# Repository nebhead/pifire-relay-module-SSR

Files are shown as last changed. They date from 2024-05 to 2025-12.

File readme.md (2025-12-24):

# PiFire Solid State Relay (SSR) Module PCB (v1.0.2) KiCad Files

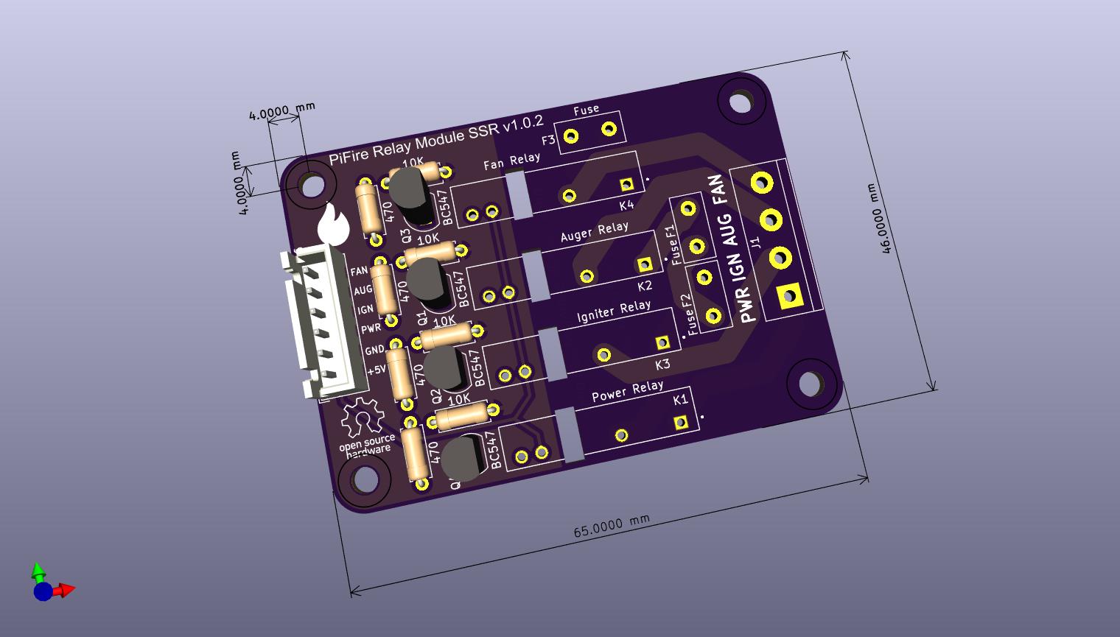
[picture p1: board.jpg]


## What is this? 

This PCB is designed to support mechanical relays for controlling incoming Power(L) to the Igniter, Auger, and AC Fan.  This board uses compact solid state relays that are able to handle high power. This is an alternative to using an off the shelf relay module which simplifies the wiring and even allows you to use the OEM harness.  

The design intent for this board was to make a DIY accessible PCB that can be more easily put together by the maker/enthusiast of almost any skill level.  Full size components are used in most cases and most (if not all) parts should be readily available to order online.  See the [Interactive BOM](#interactive-bom) for more details about the parts used and links to order.

### What is PiFire? 

PiFire is a SBC based Pellet Smoker Controller.  More details can be found [here](https://nebhead.github.io/PiFire) or [at the GitHub repo](https://github.com/nebhead/pifire). 

## What's in this Repository?

### KiCad Project Files 
In this repository you will find the latest KiCad design files for the  PCB.  Simply load the project file (.kicad_pro) into the KiCad software and you should be able to edit as needed.  Or if you just want to get this board made, jump to the production section below.

### Interactive BOM

There is an interactive BOM located in the [/bom](bom/) folder which details the parts and provides some pin information as well.  Use this to gather the components you may need to build this board out and refer back to it for placement help.    

[BOM + Pin Info](https://nebhead.github.io/pifire-relay-module-SSR)

_This is a standalone HTML file that was autogenerated by the excellent plugin for KiCad. See the plugin here: [https://github.com/openscopeproject/InteractiveHtmlBom](https://github.com/openscopeproject/InteractiveHtmlBom)_

### PDF of the Schematic

Preview the schematic in PDF format here: [Schematic](schematic.pdf)

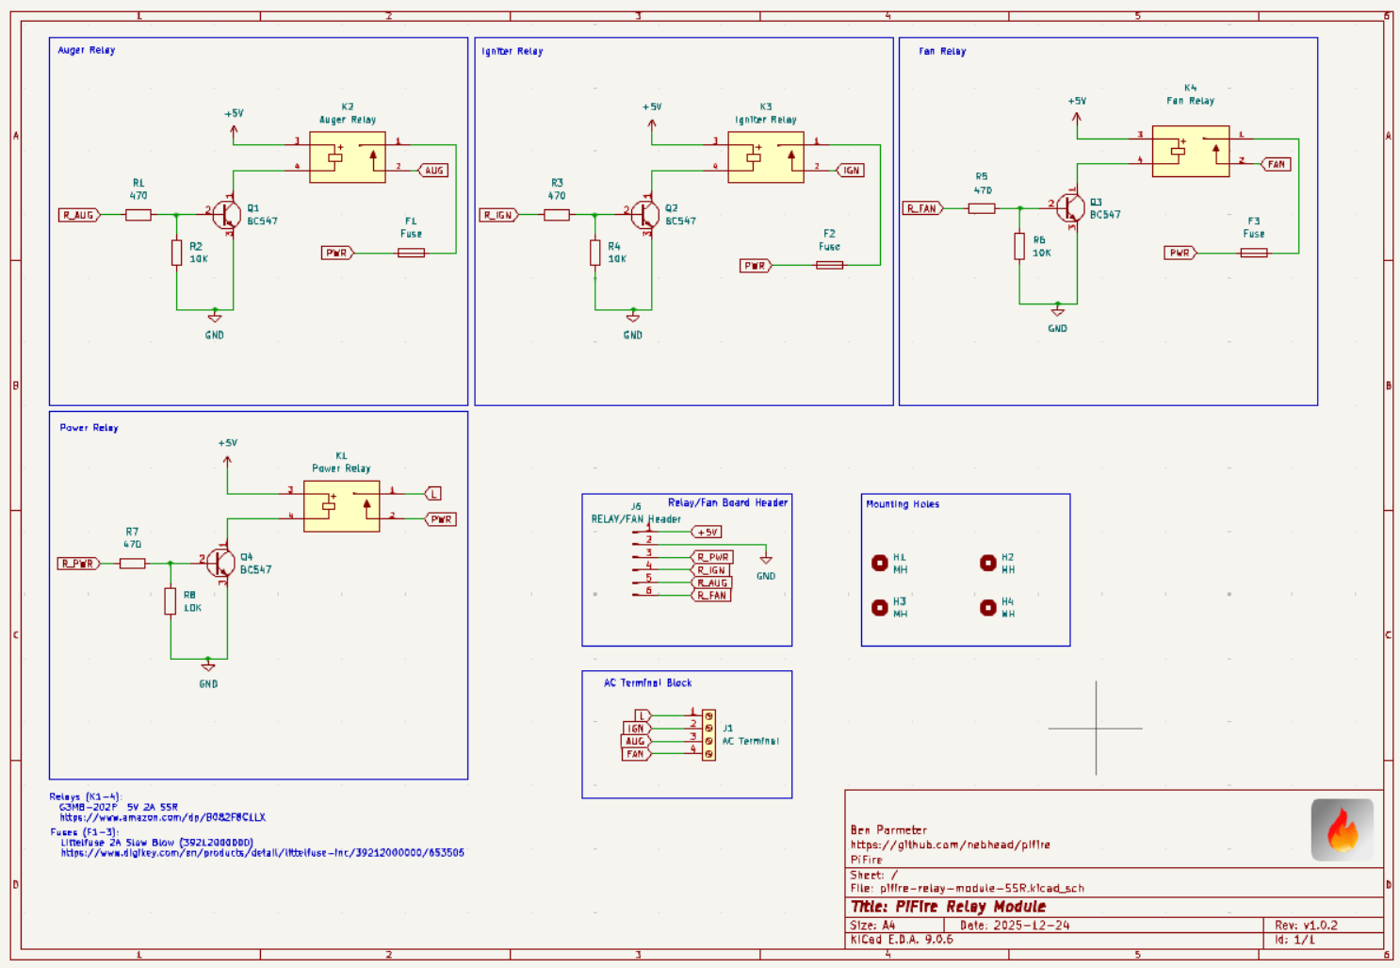
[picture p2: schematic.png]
Schematic PNG


### JLCPCB Production Files

If you wish to get these PCBs made by JLCPCB, the production files are provided in the `/production` folder.  For convenience, the file `production.zip` can simply be uploaded to JLCPCB to make it super easy to order boards.

Drop the zip file onto the order page, wait for it to upload then simply continue to order the board.  Optionally, select different board color, PCB quantity, surface finish, etc.  Most of the default settings should be sufficient. 

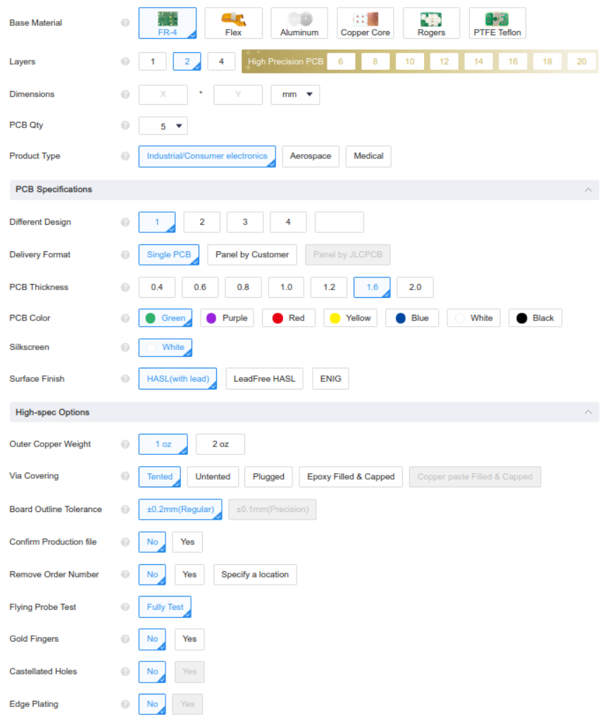
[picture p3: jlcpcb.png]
JLCPCB Order Page


### Links to the PCBs in this family of PiFire Boards

This PCB is part of a family of PCBs that can be used together to create  a full PiFire system.  Generally speaking you need the Main Module/Board, a Relay Control Board and a Probe Device board to have a basic PiFire system.  

**Main Module/Board** (required)
* [Main Board v4.0.x](https://github.com/nebhead/pifire-main-module-nopwr)

**Relay/Fan Control Boards** (choose one)
* [Mechanical Relay Module](https://github.com/nebhead/pifire-relay-module)
* [Solid State Relay Module](https://github.com/nebhead/pifire-relay-module-ssr)
* [Solid State Relay + PWM Fan Module](https://github.com/nebhead/pifire-relay-pwm-module-ssr) - Original Design
* [Solid State Relay + PWM Fan Module Alternate](https://github.com/nebhead/pifire-relay-pwm-module-ssr-alt) - Updated Design (Designed with help from @labmonkeyrat on Discord)

**Probe Device Board** (optional)
* [ADS Board](https://github.com/nebhead/pifire-ads-board) 

### 3D Printable Enclosures/Boxes 

With all of the 3D Prints for PiFire, a higher temperature filament such as PETG should be used.  PLA generally won't stand up to the temperatures that the components may be exposed to outdoors and near a hot smoker.  

#### Enclosure

Included here is an initial revision of the enclosure for this PCB.  The current models should be considered still in development and may have alignment challenges, etc. 

Except for the mounting wings, the majority of bolts to be used with this enclosure are M3. 

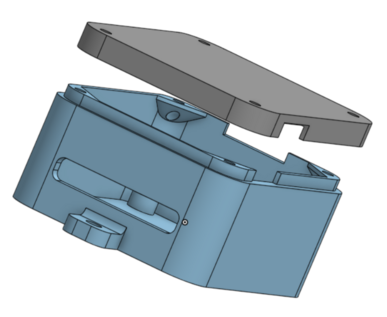
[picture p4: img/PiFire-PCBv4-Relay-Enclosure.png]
Enclosure


* STL: [Base](/printables/PiFire-v4-Relay-Base.stl)
* STL: [Lid](/printables/PiFire-v4-Relay-Lid.stl)
* OnShape: [Enclosure Original Models](https://cad.onshape.com/documents/03559f76f7adf190bf6f1259/w/7529cb0e4cd69db1a6a15202/e/07d5f9d46dc8f2b9e7dd655f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)

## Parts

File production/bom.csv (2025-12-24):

Designator | Footprint | Quantity | Value | LCSC Part #
F1, F2, F3 | Fuse_Littelfuse_395Series | 3 | Fuse
H1, H2, H3, H4 | MountingHole_3.2mm_M3 | 4 | MH
J1 | TerminalBlock_bornier-4_P5.08mm | 1 | AC Terminal
J6 | JST_XH_B6B-XH-A_1x06_P2.50mm_Vertical | 1 | RELAY/FAN Header
K1 | RELAY_G3MB-202PDC5 | 1 | Power Relay
K2 | RELAY_G3MB-202PDC5 | 1 | Auger Relay
K3 | RELAY_G3MB-202PDC5 | 1 | Igniter Relay
K4 | RELAY_G3MB-202PDC5 | 1 | Fan Relay
Q1, Q2, Q3, Q4 | TO-92L_Inline | 4 | BC547
R1, R3, R5, R7 | R_Axial_DIN0207_L6.3mm_D2.5mm_P7.62mm_Horizontal | 4 | 470
R2, R4, R6, R8 | R_Axial_DIN0207_L6.3mm_D2.5mm_P7.62mm_Horizontal | 4 | 10K

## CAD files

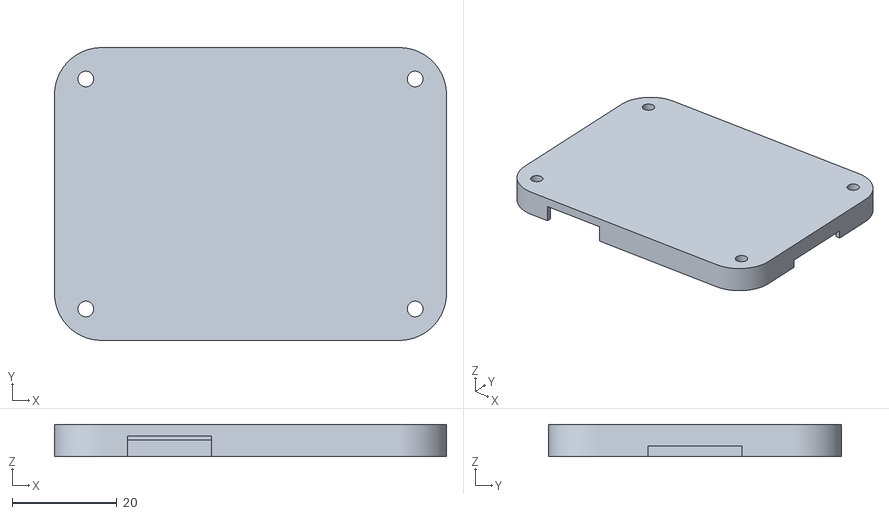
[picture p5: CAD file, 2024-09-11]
printables/PiFire-v4-Relay-Lid.stl
75.0 x 56.0 x 6.20

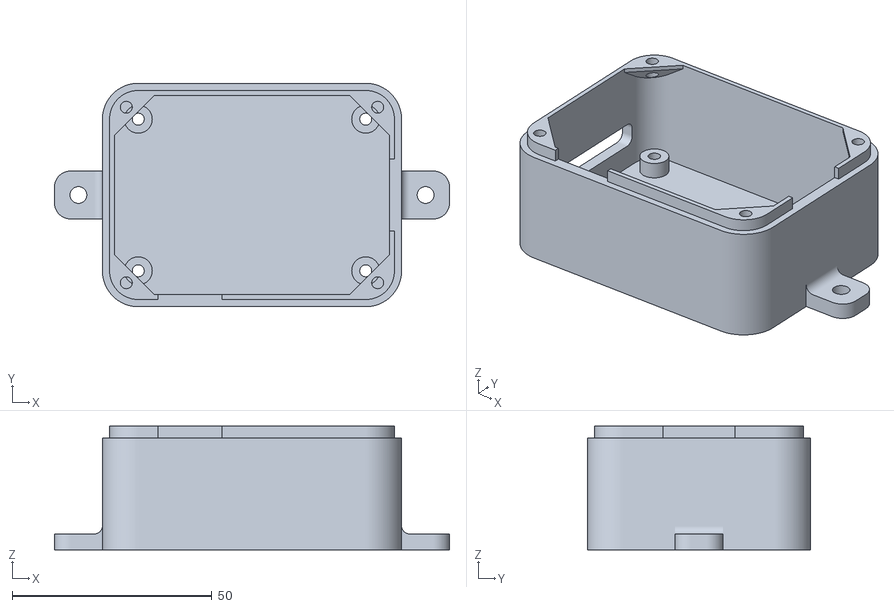
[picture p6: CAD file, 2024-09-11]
printables/PiFire-v4-Relay-Base.stl
99.0 x 56.0 x 31.0

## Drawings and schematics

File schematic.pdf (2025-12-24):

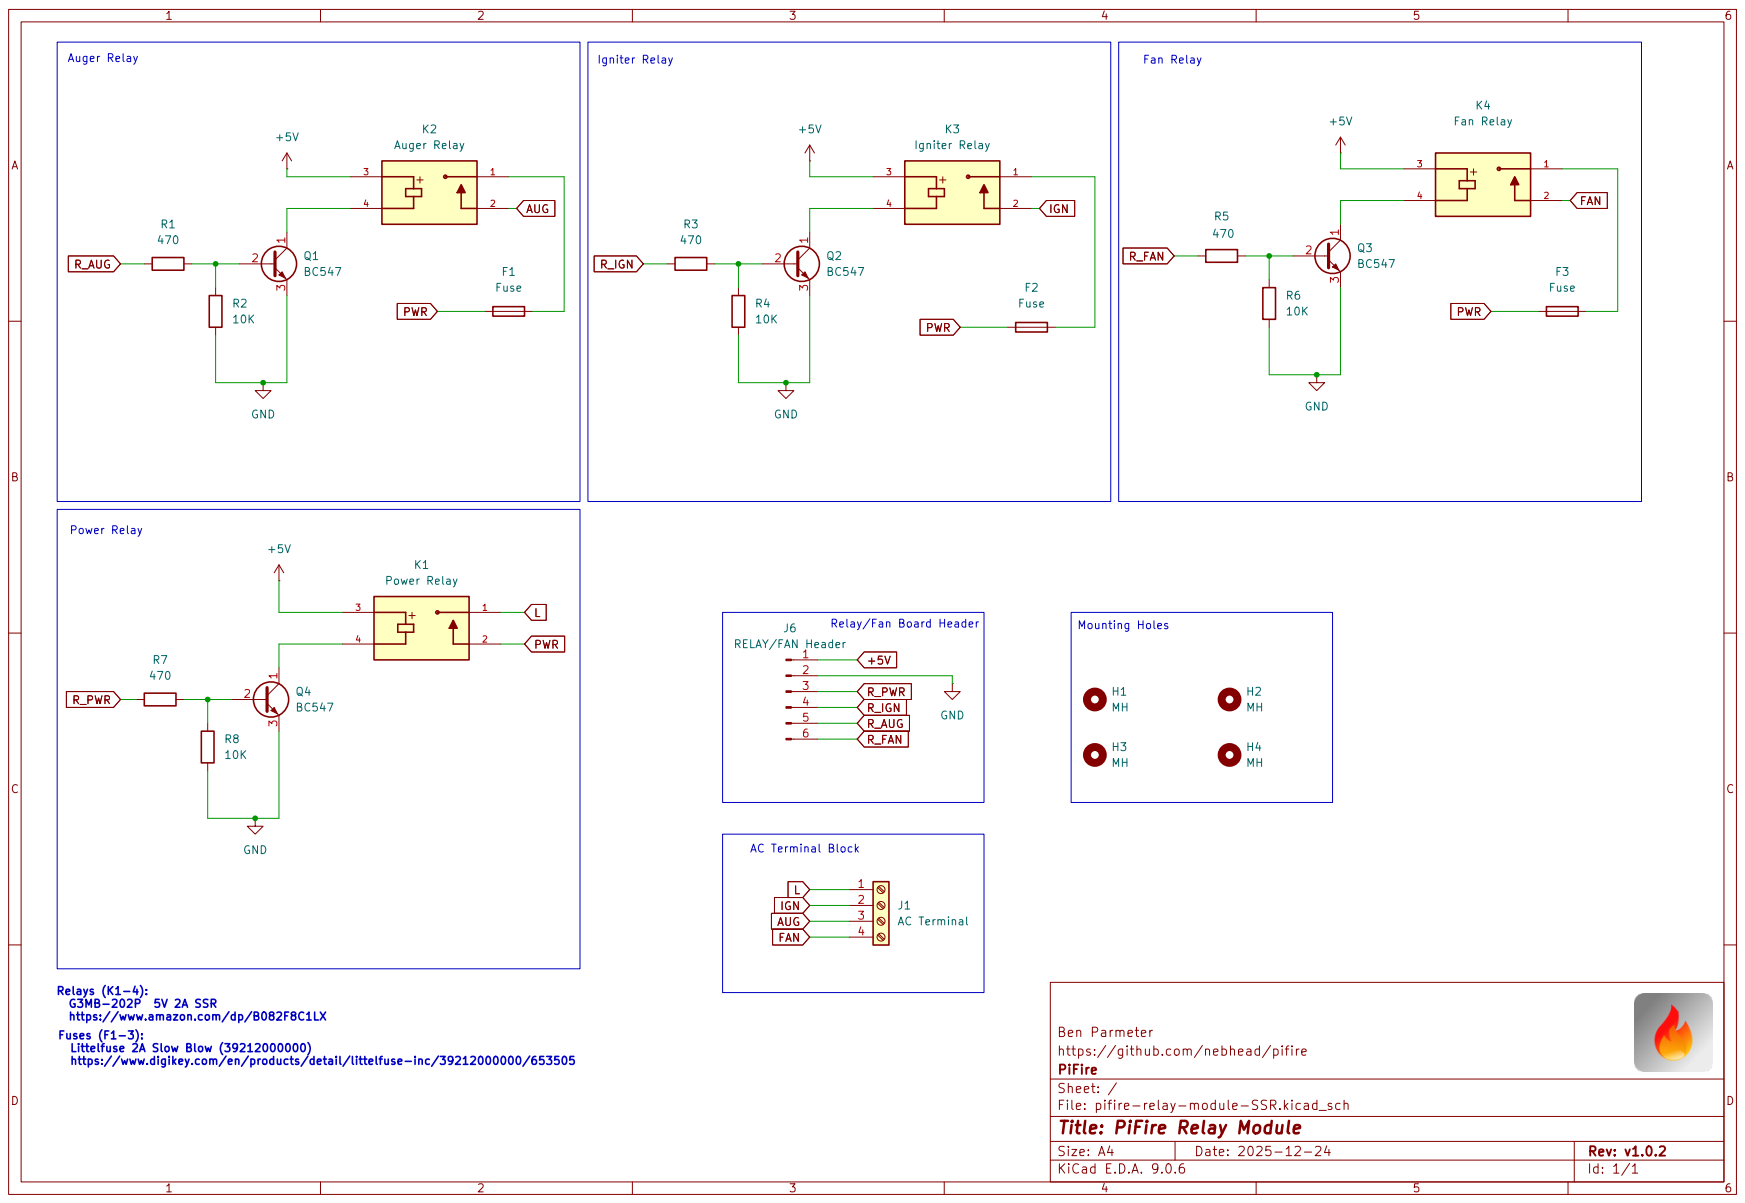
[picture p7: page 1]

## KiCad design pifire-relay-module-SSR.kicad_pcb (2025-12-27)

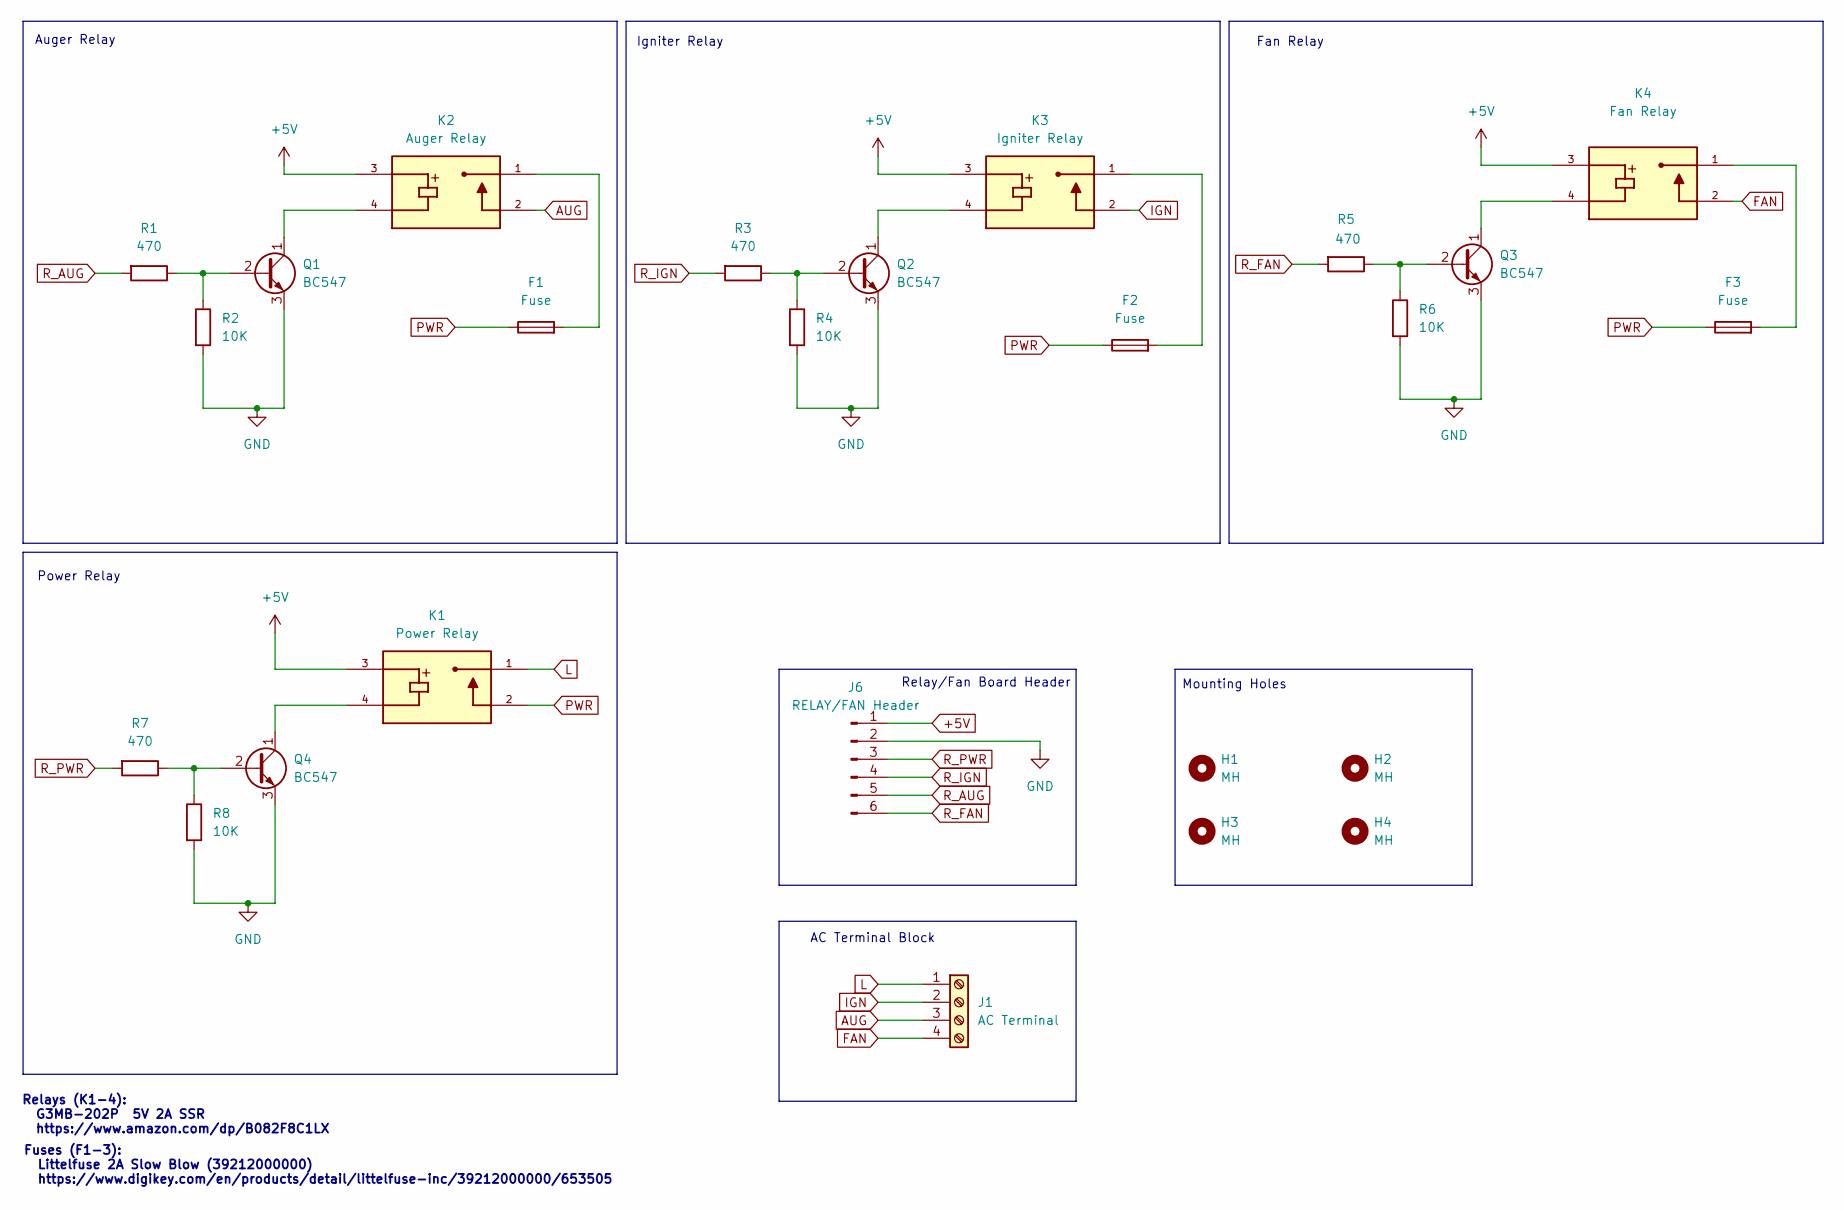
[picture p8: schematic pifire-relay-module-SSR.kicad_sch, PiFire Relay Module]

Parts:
F1, F2, F3: Fuse; Fuse_Littelfuse_395Series
H1, H2, H3, H4: MH; MountingHole_3.2mm_M3
J1: AC Terminal; TerminalBlock_bornier-4_P5.08mm
J6: RELAY/FAN Header; JST_XH_B6B-XH-A_1x06_P2.50mm_Vertical
K1: Power Relay; RELAY_G3MB-202PDC5; PARTREV J091-E1-1A
K2: Auger Relay; RELAY_G3MB-202PDC5; PARTREV J091-E1-1A
K3: Igniter Relay; RELAY_G3MB-202PDC5; PARTREV J091-E1-1A
K4: Fan Relay; RELAY_G3MB-202PDC5; PARTREV J091-E1-1A
Q1, Q2, Q3, Q4: BC547; TO-92L_Inline
R1, R3, R5, R7: 470; R_Axial_DIN0207_L6.3mm_D2.5mm_P7.62mm_Horizontal
R2, R4, R6, R8: 10K; R_Axial_DIN0207_L6.3mm_D2.5mm_P7.62mm_Horizontal

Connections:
+5V: J6.1, K1.3, K2.3, K3.3, K4.3
AUG: J1.3, K2.2
FAN: J1.4, K4.2
GND: J6.2, Q1.3 (E), Q2.3 (E), Q3.3 (E), Q4.3 (E), R2.2, R4.2, R6.2, R8.2
IGN: J1.2, K3.2
L: J1.1, K1.1
unnamed: F1.2, K2.1
unnamed: F2.2, K3.1
unnamed: F3.2, K4.1
unnamed: Q1.2 (B), R1.1, R2.1
unnamed: K2.4, Q1.1 (C)
unnamed: Q2.2 (B), R3.1, R4.1
unnamed: K3.4, Q2.1 (C)
unnamed: Q3.2 (B), R5.1, R6.1
unnamed: K4.4, Q3.1 (C)
unnamed: Q4.2 (B), R7.1, R8.1
unnamed: K1.4, Q4.1 (C)
PWR: F1.1, F2.1, F3.1, K1.2
R_AUG: J6.5, R1.2
R_FAN: J6.6, R5.2
R_IGN: J6.4, R3.2
R_PWR: J6.3, R7.2

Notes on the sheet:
Fan Relay
Power Relay
Fuses (F1-3): Littelfuse 2A Slow Blow (39212000000) https://www.digikey.com/en/products/detail/littelfuse-inc/39212000000/653505
AC Terminal Block
Auger Relay
Relay/Fan Board Header
Relays (K1-4): G3MB-202P 5V 2A SSR https://www.amazon.com/dp/B082F8C1LX
Mounting Holes
Igniter Relay

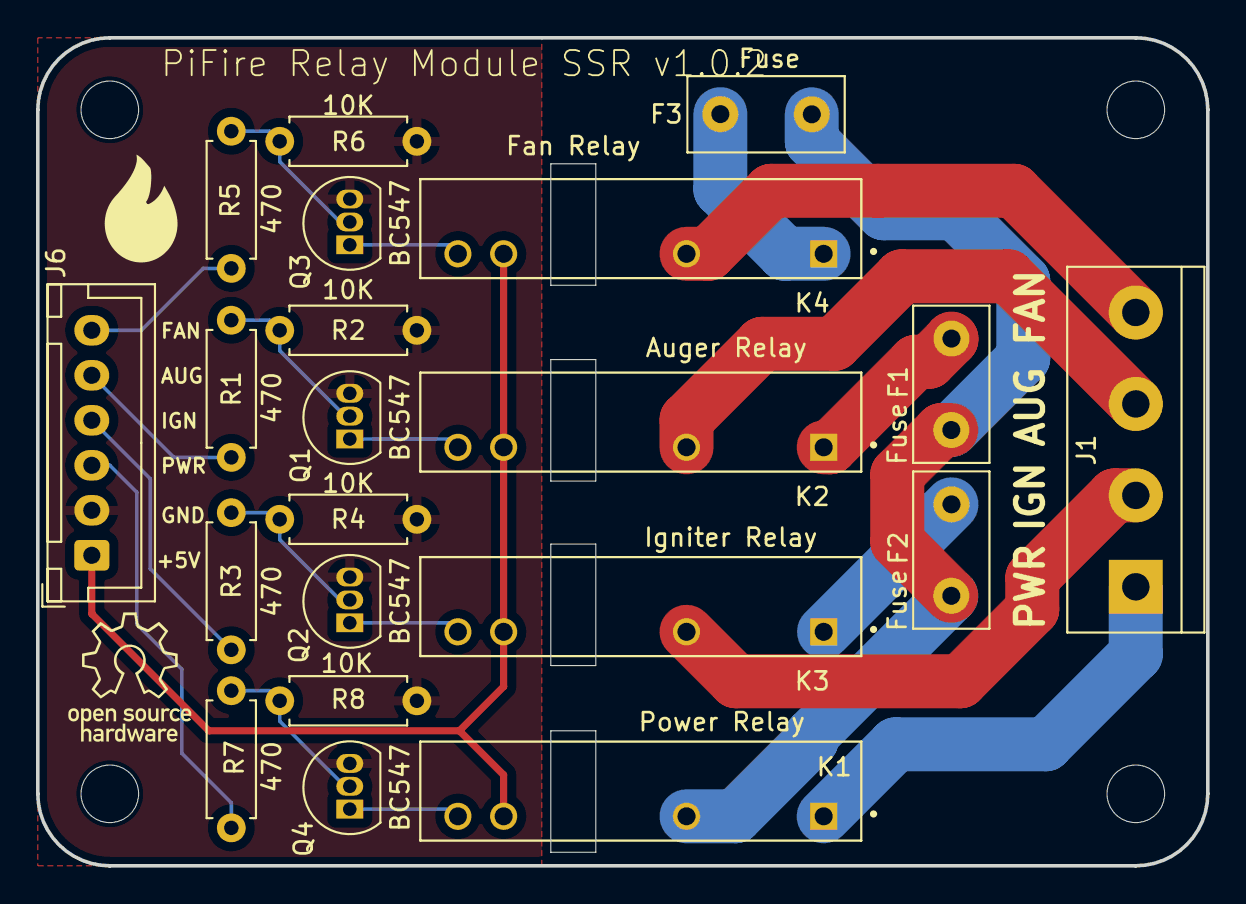
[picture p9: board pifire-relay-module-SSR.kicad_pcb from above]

Board: 2 copper layers, 65.0 x 46.0 mm, 25 parts (0 on the bottom side), 22 nets.

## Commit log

2024-05-10 Fix link to bom html
2024-05-10 Fix link to bom
2024-09-07 Update readme.md
    Update links for PWM boards.
2024-09-11 Auto stash before merge of "main" and "origin/main"
    [PiFire-v4-Relay-Base.stl, PiFire-v4-Relay-Lid.stl]
2025-12-24 Updated to V1.0.2
    This version is a minor update to change 4.7k Ohm resistor values to 470 Ohms. Some users had pointed out that the 4.7k Ohm resistors may be too large and may not allow the transistors to properly turn on. This should fix that issue.
    [bom.csv, designators.csv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]
2025-12-27 Updated v1.0.2 December on backside
    [pifire-relay-module-SSR-B_Cu.gbl, pifire-relay-module-SSR-B_Mask.gbs, pifire-relay-module-SSR-B_Paste.gbp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]
